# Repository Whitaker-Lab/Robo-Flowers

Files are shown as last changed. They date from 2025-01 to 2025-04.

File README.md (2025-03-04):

# Robo-Flowers

### A project to design and document robotic flowers to assist in studying the interactions between plants and pollinators. 

---

## 📋 Project Overview
This repository contains all resources, files, and documentation for the Robo-Flowers project.
The goal of this project is to create robotic flowers to simulate floral environments for experiments, such as testing pollinator behavior, predation risk, or other ecological interactions.

---

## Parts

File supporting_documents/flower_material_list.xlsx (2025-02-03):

Raspberry Pi Related Hardware | Description | # per Flower | Brand | Link
Raspberry Pi Zero WH | Flower Computer | 1 | Raspberry Pi | https://www.adafruit.com/product/3708
PNY 32GB Elite Class 10 U1 Micro SD card | Stores the Raspberry Pi operating system | 1 | PNY | Amazon.com: PNY 32GB Elite Class 10 U1 microSDHC Flash Memory Card - 100MB/s, Class 10, U1, Full HD, UHS-I, Micro SD (Pack of 3) : Electronics (https://www.amazon.com/PNY-Elite-microSDHC-Memory-3-Pack/dp/B07YXJM282?sp_csd=d2lkZ2V0TmFtZT1zcF9hdGY)
5 V 2.5 amp Power supply | Porwer cord for pi zero | 1 | GEAO TECHNOLOGY CO., LTD | 5V 2.5A Switching Power Supply with 20AWG MicroUSB Cable : ID 1995 : Adafruit Industries, Unique & fun DIY electronics and kits (https://www.adafruit.com/product/1995)
Ultra Tiny USB Camera with GC0307 Sensor | Camera | 1 | Shenzhen Huibo Shijie Technology | https://www.adafruit.com/product/5733
IR Break Beam Sensors with Premium Wire Header Ends - 3mm LEDs | Detects and records pollinato feeding | 1 | Adafruit | https://www.adafruit.com/product/2167#description
30cm Long Female to Female Header Jumper Wire Dupont Cable | Connect sensors to Pi | 5 | Dupont | Amazon.com: Chanzon 40pcs 30cm Long Female to Female Header Jumper Wire Dupont Cable Line Connector 40 pin Solderless Multicolored for Arduino Raspberry pi Electronic Breadboard Protoboard PCB Board : Electronics (https://www.amazon.com/dp/B09FP74HVH/ref=twister_B09G946VCF?_encoding=UTF8&th=1)
Raspberry Pi 5 Cana Kit | Central Control System | 1 per system | Raspberry Pi | https://www.amazon.com/gp/product/B0CRSNCJ6Y/ref=ppx_yo_dt_b_search_asin_title?ie=UTF8&th=1
Computer Peripherals | Monitor mouse etc to interact with Pi 5 | as needed for Pi 5 | Any
Spider System Related Hardware
Arduino Nano | Controls Spider sensors and arms | 1 | Elegoo | Amazon.com: ELEGOO Pre-soldered Nano Board CH 340/ATmega+328P with USB Cable Compatible with Arduino : Electronics (https://www.amazon.com/ELEGOO-Pre-soldered-ATmega-Compatible-Arduino/dp/B0D5LYFRQP?cv_ct_cx=arduino+nano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)
SG90 Micro Servo Motor | Controls Spider arms | 2 | WWZMDiB | https://www.amazon.com/dp/B0BKPL2Y21?ref=ppx_yo2ov_dt_b_fed_asin_title
Strain Gauge | Sense bee | 1 | Any | Amazon.com: Hemobllo Strain Gauge Bending Test Sensor Module Charge Amplifier Voltage Output : Industrial & Scientific (https://www.amazon.com/dp/B07KG6F7T3?s=industrial&sp_csd=d2lkZ2V0TmFtZT1zcF9kZXRhaWw)
3D Printing Equipment
HATCHBOX 1.75mm Green PLA 3D Printer Filament | Used to make flower stem |  | HATCHBOX | https://www.amazon.com/dp/B00J0GQ2OS/ref=twister_B09WW4Z413?_encoding=UTF8&psc=1
HATCHBOX 1.75mm Baby Blue PLA 3D Printer Filament (https://www.amazon.com/HATCHBOX-3D-Filament-Dimensional-Accuracy/dp/B0BM53T4FC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) | Used for flower top and camera stem |  | HATCHBOX | Amazon.com: HATCHBOX PLA PRO+ 3D Printer Filament, Dimensional Accuracy +/- 0.03 mm, 1 kg Spool, 1.75 mm, Baby Blue : Industrial & Scientific (https://www.amazon.com/HATCHBOX-3D-Filament-Dimensional-Accuracy/dp/B0BM53T4FC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)
HATCHBOX 1.75mm Yellow PLA 3D Printer Filament | Used for flower top and camera stem |  | HATCHBOX | https://www.amazon.com/dp/B0BM53KZDZ/ref=twister_B0BM52HX22?_encoding=UTF8&psc=1
Clear 3D Printer Resin | Used for nectar cup and spider body |  | Siraya Tech | Amazon.com: Siraya Tech Craft Ultra-Clear 3D Printer Resin - High Transparency, Non-Yellowing, 405nm Rapid Curing for LCD/DLP/8K 3D Printers, Designed for Craft Projects (1kg, High Clear) : Industrial & Scientific (https://www.amazon.com/Siraya-Tech-Ultra-Clear-Non-Yellow-Transparency/dp/B09LQW7RHX)
Resin 3d printer | Used to print Resin components |  | Any
FDM 3d printer | Used to print flower body and tops
Heating System
Nichrome Foil | Used as the heating element | 1 | Any | Amazon.com: uxcell 1M 3.3Ft 0.2x12mm Nichrome Flat Heater Wire for Heating Elements : Industrial & Scientific (https://www.amazon.com/gp/product/B01E60A20M/ref=ox_sc_act_title_3?smid=A1THAZDOWP300U&psc=1)
12 gauge wire | Electricity to heating element. | 1 | Any
Kapton Tape |  | 1 | MYJOR | MYJOR Brand High Temperature Tissue Paper Tape, Used to Protect CPU and 3D Printer Work Surface, PCB Circuit Board Professionals (1.2" x 108ft x 1): Amazon.com: Industrial & Scientific (https://www.amazon.com/Temperature-Kapton-Professional-Protecting-Circuit/dp/B07S2219CK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)
LRS-200 |  | 1 per 5 flowers |  | https://www.amazon.com/MEAN-WELL-LRS-200-24-211-2W-Switchable/dp/B00YMA7I7C?s=electronics
Power cord |  | 1 per LRS-200 | Any | https://www.amazon.com/dp/B0000510ZO?ref=ppx_yo2ov_dt_b_product_details&th=1
Socket |  | 1 per LRS-200 | Any | https://www.amazon.com/dp/B07RRY5MYZ?psc=1&ref=ppx_yo2ov_dt_b_product_details
K Type Thermocouple |  | 1 | HiLetgo | HiLetgo DC 3-5V MAX6675 Module + K Type Thermocouple Temperature Sensor Thermocouple Sensor Set M6 Screw for Arduino: Amazon.com: Industrial & Scientific (https://www.amazon.com/dp/B01HT871SO?ref=ppx_yo2ov_dt_b_fed_asin_title)

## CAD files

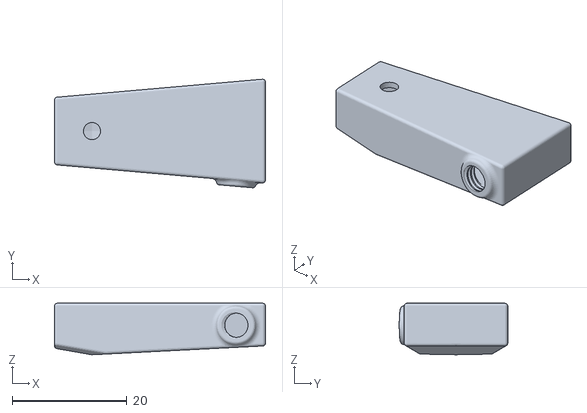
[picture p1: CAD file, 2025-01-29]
Flower_stls/Reservoir.stl
36.8 x 19.0 x 9.00

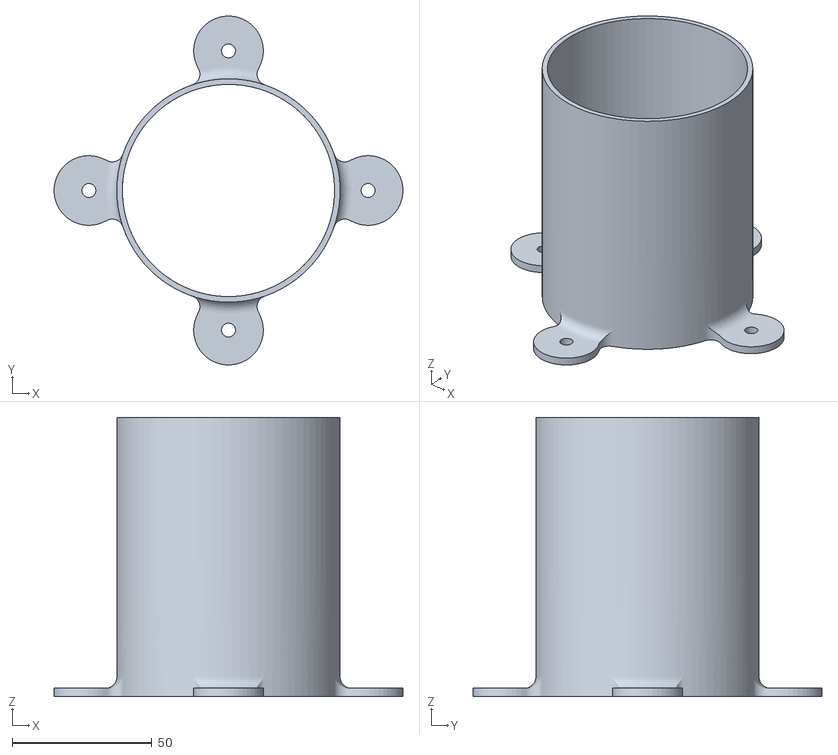
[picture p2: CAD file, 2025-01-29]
Flower_stls/Flower Base.stl
125.0 x 125.0 x 100.0

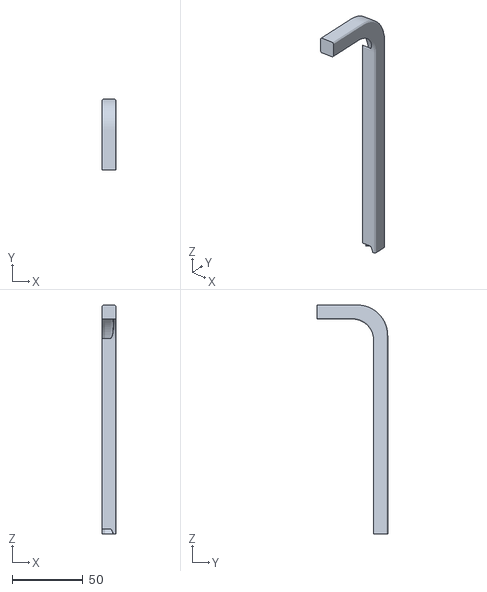
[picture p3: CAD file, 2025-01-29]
Flower_stls/CameraStalk.stl
10.0 x 50.0 x 162.4

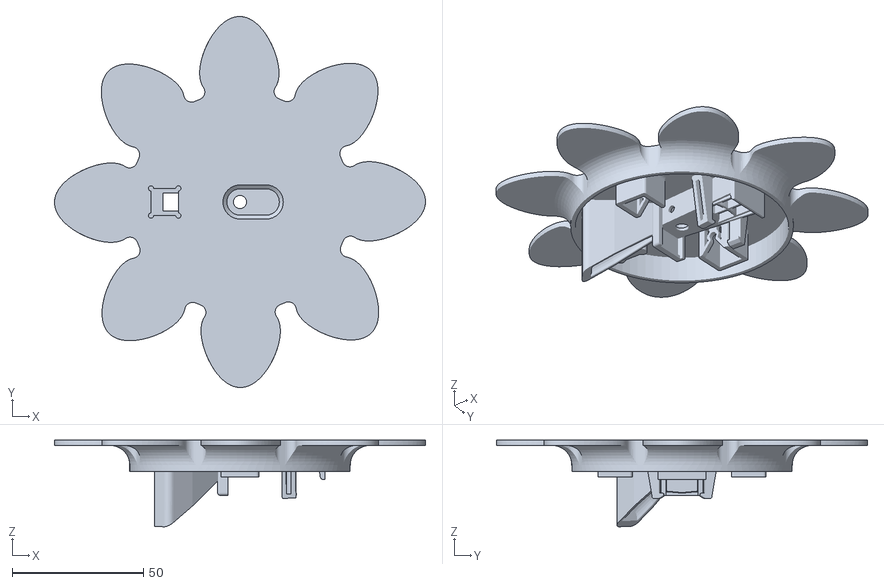
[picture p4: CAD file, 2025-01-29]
Flower_stls/Flower Top.stl
141.3 x 141.3 x 33.0

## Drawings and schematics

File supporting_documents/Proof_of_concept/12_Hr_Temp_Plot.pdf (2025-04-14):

## Temperature Over a 12 Hour Run

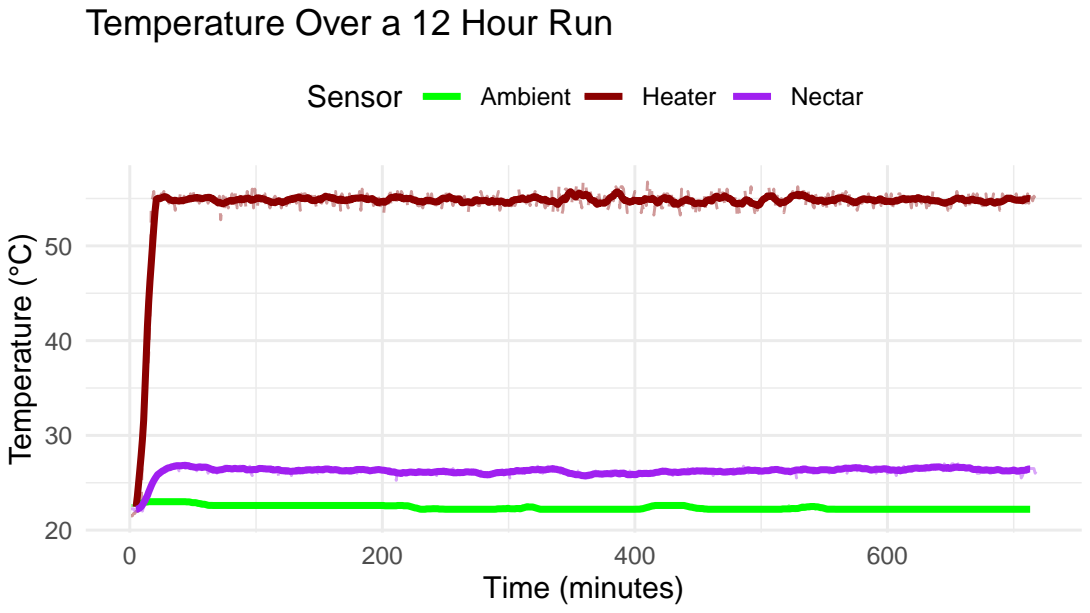
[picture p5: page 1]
Time (minutes); Temperature (°C); Sensor; Ambient; Heater; Nectar

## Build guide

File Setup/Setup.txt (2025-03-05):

This project uses RapsberryPi Zero WHs running the 32-bit Bookworm Lite OS (November 2024 release). Wifi credentials and ssh are enabled during SD card formatting. Once the pis are booted and connected to wifi, they can be accessed via ssh and set up by sending and executing the NewPiSetup.sh script (Operating Code) on each pi.

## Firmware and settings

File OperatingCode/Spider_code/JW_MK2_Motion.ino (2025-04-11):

#include <Servo.h>

Servo servo1;
Servo servo2;

const int pirPin = 2;     // PIR output pin
const int servoPin1 = 9;  // Servo 1
const int servoPin2 = 10; // Servo 2
bool triggered = false;

void setup() {
  Serial.begin(9600);

  pinMode(pirPin, INPUT);
  servo1.attach(servoPin1);
  servo2.attach(servoPin2);

  servo1.write(0);
  servo2.write(90);  // Assuming mirrored
}

void loop() {
  int motion = digitalRead(pirPin);

  if (motion == HIGH && !triggered) {
    Serial.println("Motion detected!");
    triggered = true;

    for (int angle = 0; angle <= 90; angle++) {
      servo1.write(angle);
      servo2.write(90 - angle);
      delay(15);
    }

    delay(500); // Hold

    for (int angle = 90; angle >= 0; angle--) {
      servo1.write(angle);
      servo2.write(90 - angle);
      delay(15);
    }
  }

  if (motion == LOW) {
    triggered = false; // Reset state when motion ends
  }

  delay(100); // debounce-ish
}

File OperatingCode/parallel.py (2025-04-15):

import os
import sys
import time
import argparse
from datetime import datetime
import subprocess
import logging
import pandas as pd
from concurrent.futures import ThreadPoolExecutor

# Script paths (local machine)
IRScript = '/home/rpimain/Scripts/IR_Recording.py'
CameraScript = '/home/rpimain/Scripts/20241114_Camera.py'
RollCallScript = '/home/rpimain/Scripts/BetterRollCall.py'

def get_pi_credentials(pi_num):
    username = f"pi{pi_num}"
    hostname = f"{username}.wifi.etsu.edu"
    return username, hostname

def check_file_exists(pi_num, remote_path):
    username, hostname = get_pi_credentials(pi_num)
    check_command = f"ssh {username}@{hostname} '[ -f {remote_path} ] && echo Exists || echo Missing'"
    try:
        result = subprocess.check_output(check_command, shell=True, text=True).strip()
        return result == "Exists"
    except subprocess.CalledProcessError:
        return False

def send_scripts_to_pi(pi_num, ir_only=False):
    username, hostname = get_pi_credentials(pi_num)
    scripts_to_send = [(IRScript, "IR_Recording.py")]
    if not ir_only:
        scripts_to_send.append((CameraScript, "CameraScript.py"))

    for script, remote_name in scripts_to_send:
        remote_path = f"/home/{username}/{remote_name}"
        if not check_file_exists(pi_num, remote_path):
            try:
                scp_command = f"scp {script} {username}@{hostname}:{remote_path}"
                subprocess.check_call(scp_command, shell=True)
                print(f"{remote_name} sent to {hostname}.")
                logging.info(f"{remote_name} sent to {hostname}.")
            except subprocess.CalledProcessError as e:
                print(f"Error sending {remote_name} to {hostname}: {e}")
                logging.error(f"Error sending {remote_name} to {hostname}: {e}")

def execute_scripts_on_pi(pi_num, ir_only=False):
    username, hostname = get_pi_credentials(pi_num)
    commands = []
    commands.append((
        f"screen -dmS IRScript_{pi_num} bash -c 'mkdir -p Logs; python3 IR_Recording.py > Logs/IR_Recording.log 2>&1'",
        "IR_Recording.py"
    ))
    if not ir_only:
        commands.append((
            f"screen -dmS CameraScript_{pi_num} bash -c 'mkdir -p Logs; python3 CameraScript.py > Logs/CameraScript.log 2>&1'",
            "CameraScript.py"
        ))

    try:
        for cmd, script_name in commands:
            ssh_command = f"ssh {username}@{hostname} \"{cmd}\""
            subprocess.check_call(ssh_command, shell=True)
            print(f"{script_name} successfully started on {hostname}.")
            logging.info(f"{script_name} successfully started on {hostname}.")
    except subprocess.CalledProcessError as e:
        print(f"Error executing scripts on {hostname}: {e}")
        logging.error(f"Error executing scripts on {hostname}: {e}")

def fetch_csv_files(pi_hosts, base_local_directory):
    current_date = datetime.now().strftime("%Y-%m-%d")
    local_directory = os.path.join(base_local_directory, current_date)
    os.makedirs(local_directory, exist_ok=True)

    print("\nFetching CSV files from remote Pis...")
    failed_fetches = []

    def fetch_from_host(host):
        user = host.split('.')[0]
        remote_directory = f"/home/{user}/Data"
        try:
            subprocess.run([
                "scp", f"{user}@{host}:{remote_directory}/{current_date}*.csv", local_directory
            ], check=True)
            print(f"Fetched files from {host}.")
        except subprocess.CalledProcessError:
            print(f"Error fetching files from {host}.")
            failed_fetches.append(host)

    with ThreadPoolExecutor(max_workers=10) as executor:
        executor.map(fetch_from_host, pi_hosts)

    if failed_fetches:
        print("\nThe following Pis failed to transfer CSV files:")
        for failed_host in failed_fetches:
            print(failed_host)

def cleanup(pi_hosts):
    print("\nPerforming cleanup...")

    def cleanup_host(host):
        user = host.split('.')[0]
        try:
            subprocess.run(["ssh", f"{user}@{host}", "pkill screen"], check=True)
            print(f"Screen sessions terminated on {host}.")
        except subprocess.CalledProcessError:
            print(f"Error terminating screen sessions on {host}.")

    with ThreadPoolExecutor(max_workers=10) as executor:
        executor.map(cleanup_host, pi_hosts)

if __name__ == "__main__":
    parser = argparse.ArgumentParser(description="Control script for sending/executing IR and Camera scripts on Pis.")
    parser.add_argument('--ir-only', action='store_true', help='Only run the IR script (skip Camera script)')
    args = parser.parse_args()

    pi_hosts = [f"pi{i}.wifi.etsu.edu" for i in range(1, 21)]
    current_date = datetime.now().strftime("%Y-%m-%d")
    current_time = datetime.now().strftime("%H%M%S")

    local_directory = "/home/rpimain/Data"

    logging.basicConfig(level=logging.INFO, format='%(asctime)s %(levelname)s: %(message)s', handlers=[
        logging.StreamHandler(sys.stdout)
    ])

    try:
        subprocess.check_call(["python3", RollCallScript])
    except subprocess.CalledProcessError:
        print("Roll call failed. Halting execution.")
        sys.exit(1)

    with ThreadPoolExecutor(max_workers=10) as executor:
        for pi_num in range(1, 21):
            executor.submit(send_scripts_to_pi, pi_num, args.ir_only)

    with ThreadPoolExecutor(max_workers=10) as executor:
        for pi_num in range(1, 21):
            executor.submit(execute_scripts_on_pi, pi_num, args.ir_only)

    print("All scripts started on Pis.")
    logging.info("All scripts started on Pis.")

    duration = 12 * 3600
    print("\nWaiting for 12 hours ...")
    time.sleep(duration)

    fetch_csv_files(pi_hosts, local_directory)
    cleanup(pi_hosts)

    print("All screen sessions terminated.")
    logging.info("All screen sessions terminated.")

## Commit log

2025-01-27 Add flower material list
    [flower_material_list.xlsx]
2025-01-29 Added STL files for Robo-Flowers project
    [Flower Base.stl, Flower Stem.stl, Flower Top.stl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]
2025-02-03 Create IR_Recording
    script to run the infrared break beam sensors to record bee visitation events
2025-02-03 Add files via upload
    Material list to build robotic flower field.
    [flower_material_list.xlsx]
2025-02-03 Create rollCall
    script to ping each pi to make sure they're all connected to the network and to test attached peripherals (e.g. cameras)
2025-02-03 Create ControlScript.py
    script to be run from the Central/Control pi that pushes two scripts (IR and Camera) to all peripheral pis running robot-flowers, runs the scripts for a designated period, then kills the scripts on a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
2025-02-03 Create Camera.py
    script to run a motion-triggered camera
2025-02-03 Add files via upload
    Design drawings for the flower system.
2025-02-04 Commented Camera code
2025-02-09 New camera code
2025-02-13 Updated Camera code
2025-03-04 Rename Flower Stem.stl to CameraStalk.stl
    [CameraStalk.stl]
2025-04-12 Add files via upload
    Heater 12 hour nectar temp test.
2025-04-14 Add files via upload
    Twelve hour heater verification test.
2025-04-14 Add files via upload
    Pictures of flower with insects
2025-04-15 Much faster Control script
    New control scripts sends and executes Camera and IR scripts to remote pis in parallel rather than in sequence and is therefore MUCH faster than the previous method
